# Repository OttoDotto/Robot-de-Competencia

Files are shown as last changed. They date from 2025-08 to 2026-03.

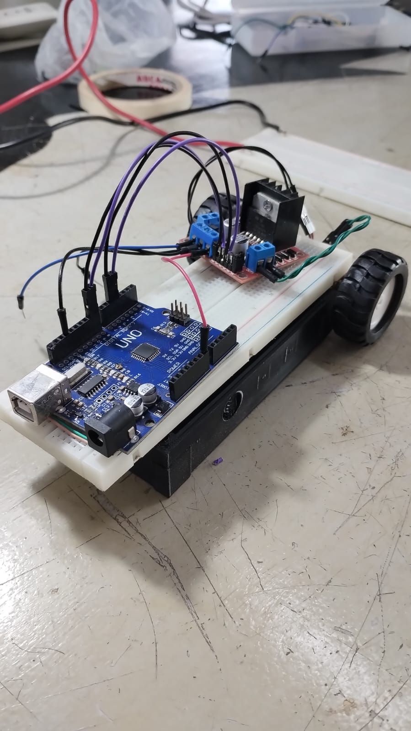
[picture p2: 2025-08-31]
Galeria/prueba_Protoboard - V0.jpg

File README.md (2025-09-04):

# Proyecto Robot de Competencia

Este repositorio contiene el diseño y desarrollo de un **robot móvil autónomo** basado en **ESP32**, pensado para competencias de **seguidores de línea** y adaptable a otras categorías (sumo o fútbol robótico).

## 🏁 Objetivo
Este proyecto representa el **primer paso de la Facultad del Ejército Argentino en el mundo de la robótica competitiva**.  
Más allá del desarrollo técnico, nuestro propósito es:  
- Introducirnos en el ámbito de las competencias robóticas estudiantiles.  
- Presentar a nuestra institución en la comunidad tecnológica.  
- Generar experiencia para futuras participaciones en categorías como seguidor de línea, fútbol robótico y sumo.  
- Sentar las bases para que, en el futuro, la Facultad pueda convertirse en **sede de competencias de robótica**.  

## 🔧 Características principales
- **Microcontrolador**: ESP32 DevKit V1
- **Motores**: 2 × DC Pololu con controladores DRV8833 en configuración paralela
- **Sensores**: Array de 8 sensores reflectivos (QTR-8A)
- **Estructura**: Base y Diseño fabricado en impresión 3D
- **Conectividad**: Bluetooth, Wi-Fi y Control con mando PS
- **Aplicaciones**:  
  - Seguidor de línea (principal)  
  - Adaptación a fútbol robótico

## 📂 Contenido del repositorio
- `/Pcb Kicad` → esquemáticos y PCB en KiCad
- `/Fabricacion` → archivos para fabricacion casera del PCB
- `/Programacion` → códigos utilizados (Motores, Sensores, etc.)
- `/Documentos` → documentación, datasheets, imágenes de referencia del proyecto
- `/Galeria` → Fotografias, videos e imagenes del proyecto

## 📸 Galería (soon tm)

## 👥 Autores
Proyecto desarrollado en la **Facultad del Ejército Argentino** por el equipo **Legión de Ohm**.

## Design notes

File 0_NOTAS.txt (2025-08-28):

git: https://github.com/OttoDotto/Robot-de-Competencia

OBJETIVO PRINCIPAL:	Armar el circuito de control del robot de competencia - Seguidor de linea, Futbolero &/o Sumo
* Separar la lectura en otra PCB
* Separar el diseño 3D aparte de las pcbs 			No hacer un T que sea una placa de cobre entera
* Simplificar el trabajo para el equipo de futbol &/o Sumo

REQUIRIMIENTOS:
* Debe tener espacio para sostener los motores o agarrarlos desde el pcb. (optimizar lugar - como en el caso de los competidores)
* Debe tener entradas para la placa de sensores. Conector plano o molex, recibe la lecturas Analógicas y los alimenta vcc&gnd
* Debe tener tira de pines para quitar o cambiar los puentesH o el uc
* Debe tener cables con un conector para alimentar la pcb
* Debe tener un regulador de tensión para alimentar desde una pila externa mediante un conector (con. cable-cable)
* Si es necesario usaremos componentes SMD
* En el caso del seguidor, vamos a usar:
	* microC	- ESP WROOM-32 DEVKIT V1
	* PUENTE H	- DRV8833			MODO PARALELO			
	* MOTORES	- MICRO POLOLU 6V 500 RPM
* Debe tener pulsadores o botones integrados en el pcb
	- Encendido del robot
	- Calibración de sensores	(leer que valores son blancos y cuales son negros - cambia con la pista)

TO-DO:
* Charlar sobre el presupuesto y tiempo a dedicar + que buscamos conseguir con la competencia	(Aprobar TD2)
* Leer los reglamentos en caso de excepciones con los componentes que usemos
* Buscar y definir que baterias vamos a utilizar
* Definir el tamaño del pcb y chasis (Trapecio)
* Buscar el modelo 3D aprox de los motores
* Buscar y definir que conectores vamos a usar
* Verificar el micro-controlador que estamos usando

DONE:
* Sensores a usar QTR-8A. Pueden trabajar con 3.3V  (Modulo de 8 sensores con 11 pines, vcc y gnd + 8 salidas Analogs + pin apagarleds)

APUNTES:
* Los sensores deben ir conectados a los ADC del ESP32
* Los puentesH deben ir conectados a tres pines, dos de control y uno de pwm
* Vin del esp32 es entre 4 y 12 V

* PINES ESP32 ELEJIDOS:	(D = GPIO !!!!)
Sensores (fila bajo el USB, contiguos para pistas rectas)
S1 → GPIO36 (VP)
S2 → GPIO39 (VN)
S3 → GPIO34
S4 → GPIO35
S5 → GPIO32
S6 → GPIO33
S7 → GPIO27
S8 → GPIO14

Puente H izquierdo (M1) – lado izquierdo del ESP32
IN1_M1 → GPIO26 (PWM)
IN2_M1 → GPIO25 (PWM)
SLEEP_M1 → GPIO16		(PROBLEMA, ESTA DEL OTRO LADO)

Puente H derecho (M2) – lado derecho del ESP32
IN1_M2 → GPIO21 (PWM)
IN2_M2 → GPIO18 (PWM)
SLEEP_M2 → GPIO23

Botones, buzzer, LED (abajo/derecha)
SW1 → GPIO22 (entrada con pull-up interno)
SW2 → GPIO19 (entrada con pull-up interno)
BUZZER → GPIO17 (PWM con LEDC)			(PROBLEMA, queda atrapado)
LED → GPIO13 (salida)

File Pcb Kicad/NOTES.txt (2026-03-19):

OBJETIVO PRINCIPAL:	Armar el circuito de control del robot de competencia - Seguidor de linea, Futbolero &/o Sumo
* Separar la lectura en otra PCB
* Separar el diseño 3D aparte de las pcbs 			No hacer un T que sea una placa de cobre entera
* Simplificar el trabajo para el equipo de futbol &/o Sumo

REQUIRIMIENTOS:
* Debe tener espacio para sostener los motores o agarrarlos desde el pcb. (optimizar lugar - como en el caso de los competidores)
* Debe tener entradas para la placa de sensores. Conector plano o molex, recibe la lecturas Analógicas y los alimenta vcc&gnd + LED_OFF(IR)
* Debe tener tira de pines para quitar o cambiar los puentesH o el uc
* Debe tener un regulador de tensión para alimentar desde una pila externa mediante un conector (con. cable-cable)
* Si es necesario usaremos componentes SMD
* En el caso del seguidor, vamos a usar:
	* microC	- ESP WROOM-32 o Arduino Nano
	* PUENTE H	- DRV8833			
	* MOTORES	- MICRO POLOLU 6V 800 RPM
* Debe tener pulsadores o botones integrados en el pcb
	- Encendido del robot
	- Calibración de sensores	(leer que valores son blancos y cuales son negros - cambia con la pista)

APUNTES:
* PINES ESP32 ELEJIDOS:	(D = GPIO !!!!)
Sensores (fila bajo el USB, contiguos para pistas rectas)
S1 → GPIO36 (VP)
S2 → GPIO39 (VN)
S3 → GPIO34
S4 → GPIO35
S5 → GPIO32
S6 → GPIO33
S7 → GPIO27
S8 → GPIO14

Puente H izquierdo (M1) – lado izquierdo del ESP32
IN1_M1 → GPIO26 (PWM)
IN2_M1 → GPIO25 (PWM)
SLEEP_M1 → GPIO16

Puente H derecho (M2) – lado derecho del ESP32
IN1_M2 → GPIO21 (PWM)
IN2_M2 → GPIO18 (PWM)
SLEEP_M2 → GPIO23

Botones, buzzer, LED (abajo/derecha)
SW1 → GPIO22 (entrada con pull-down)
SW2 → GPIO19 (entrada con pull-down)
BUZZER → GPIO17 (PWM con LEDC)
LED → GPIO13 (salida)

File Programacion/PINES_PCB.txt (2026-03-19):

* PINES ESP32 ELEJIDOS:	(D = GPIO !!!!)

📡 Sensores 
(Fila bajo el USB, contiguos para pistas rectas)
| Sensor |  Pin ESP32  | Descripción |
|---|---|---|
| S1 | GPIO36 (VP) | Entrada analógica |
| S2 | GPIO39 (VN) | Entrada analógica |
| S3 | GPIO34 | Entrada analógica |
| S4 | GPIO35 | Entrada analógica |
| S5 | GPIO32 | Entrada analógica |
| S6 | GPIO33 | Entrada analógica |
| S7 | GPIO27 | Entrada digital |
| S8 | GPIO14 | Entrada digital |

⚙️ Puente H izquierdo (M1)  
(Lado izquierdo del ESP32)
| Señal | Pin ESP32 | Función |
|---|---|---|
| IN1_M1 | GPIO26 | PWM |
| IN2_M1 | GPIO25 | PWM |
| SLEEP_M1  | GPIO16 | Control de habilitación |

⚙️ Puente H derecho (M2)  
(Lado derecho del ESP32)
| Señal | Pin ESP32 | Función |
|---|---|---|
| IN1_M2 | GPIO21 | PWM |
| IN2_M2 | GPIO18 | PWM |
| SLEEP_M2  | GPIO23 | Control de habilitación |

🔘 Botones, 🔔 Buzzer, 💡 LED, 📶 Sensor IR
| Componente | Pin ESP32 | Configuración |
|---|---|---|
| SW1 | GPIO22 | Entrada con pull-down |
| SW2 | GPIO19 | Entrada con pull-down |
| BUZZER | GPIO17 | PWM con LEDC |
| LED | GPIO13 | Salida digital |
| IR | GPIO04 | Entrada con pull-up externo |

📑 Resumen
Este documento lista los pines utilizados en el proyecto con ESP32, organizados por función:  
- Sensores de pista  
- Puentes H para control de motores (M1 y M2)  
- Botones, buzzer, LED y sensor IR

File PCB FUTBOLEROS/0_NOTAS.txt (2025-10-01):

OBJETIVO PRINCIPAL:	Armar el circuito de control del robot de competencia - Seguidor de linea, Futbolero &/o Sumo
* Separar la lectura en otra PCB
* Separar el diseño 3D aparte de las pcbs 			No hacer un T que sea una placa de cobre entera
* Simplificar el trabajo para el equipo de futbol &/o Sumo

REQUIRIMIENTOS:
* Debe tener espacio para sostener los motores o agarrarlos desde el pcb. (optimizar lugar - como en el caso de los competidores)
* Debe tener entradas para la placa de sensores. Conector plano o molex, recibe la lecturas Analógicas y los alimenta vcc&gnd + LED_OFF(IR)
* Debe tener tira de pines para quitar o cambiar los puentesH o el uc
* Debe tener un regulador de tensión para alimentar desde una pila externa mediante un conector (con. cable-cable)
* Si es necesario usaremos componentes SMD
* En el caso del seguidor, vamos a usar:
	* microC	- ESP WROOM-32 DEVKIT V1
	* PUENTE H	- DRV8833			MODO PARALELO			
	* MOTORES	- MICRO POLOLU 6V 500 RPM
* Debe tener pulsadores o botones integrados en el pcb
	- Encendido del robot
	- Calibración de sensores	(leer que valores son blancos y cuales son negros - cambia con la pista)

TO-DO:
* REVISAR EL REGULADOR DE TENSION DE LA PCB (7805 -> AMS1117) 
	- cambiar por regulador Low voltage dropout
	- 7805 SMD son 2V, MINIMO NECESITA 7V y casi 9V
	- AMS1117 SMD son 1.1V, NECESITA 6V Y CASI 7V

* REVISAR LOS BOTONES PULLDOWN (peligroso)
	1. poner una resistencia que vaya al micro
	2. cambiar por un pull down
	3. o usar pull down	(NO USAR EL PUENTE)
	4. cap de 100n (anti-rebote)

* REVISAR COMO CONECTAR LA ALIMENTACION
	- SISTEMA ANTI-PUJOL
	- CONECTOR "POLARIZADO"
	- DIODO SHOCKY EN DIRECTA

* SISTEMA MEDIDOR DE NIVEL DE BATERIA
	- Divisor de tension (8.4 a 3.3 [3.2] Volts) + Diodos de protec (BTA) o diodos simples + CAP
	- Tambien es protec de sobretension (version 2)
	- TEST POINTS [mas facil]

* Buscar el modelo 3D aprox de los motores
* Buscar y definir que conectores vamos a usar (TIRA DE PINES + )

DONE:
* Leer los reglamentos en caso de excepciones con los componentes que usemos
* Sensores a usar QTR-8A. Pueden trabajar con 3.3V  (Modulo de 8 sensores con 11 pines, vcc y gnd + 8 salidas Analogs + pin apagarleds)
* Charlar sobre el presupuesto y tiempo a dedicar + que buscamos conseguir con la competencia	(Aprobar TD2)
* Buscar y definir que baterias vamos a utilizar
* Definir el tamaño del pcb y chasis (Trapecio)
* Verificar el micro-controlador que estamos usando	(ESP WROOM 32 - DEVKIT V1 - USB C y B)

APUNTES:
* Los sensores deben ir conectados a los ADC del ESP32
* Los puentesH deben ir conectados a tres pines, dos de control y uno de pwm
* Vin del esp32 es entre 4 y 12 V
* PINES ESP32 ELEJIDOS:	(D = GPIO !!!!)
Sensores (fila bajo el USB, contiguos para pistas rectas)
S1 → GPIO36 (VP)
S2 → GPIO39 (VN)
S3 → GPIO34
S4 → GPIO35
S5 → GPIO32
S6 → GPIO33
S7 → GPIO27
S8 → GPIO14

Puente H izquierdo (M1) – lado izquierdo del ESP32
IN1_M1 → GPIO26 (PWM)
IN2_M1 → GPIO25 (PWM)
SLEEP_M1 → GPIO16

Puente H derecho (M2) – lado derecho del ESP32
IN1_M2 → GPIO21 (PWM)
IN2_M2 → GPIO18 (PWM)
SLEEP_M2 → GPIO23

Botones, buzzer, LED (abajo/derecha)
SW1 → GPIO22 (entrada con pull-down)
SW2 → GPIO19 (entrada con pull-down)
BUZZER → GPIO17 (PWM con LEDC)
LED → GPIO13 (salida)

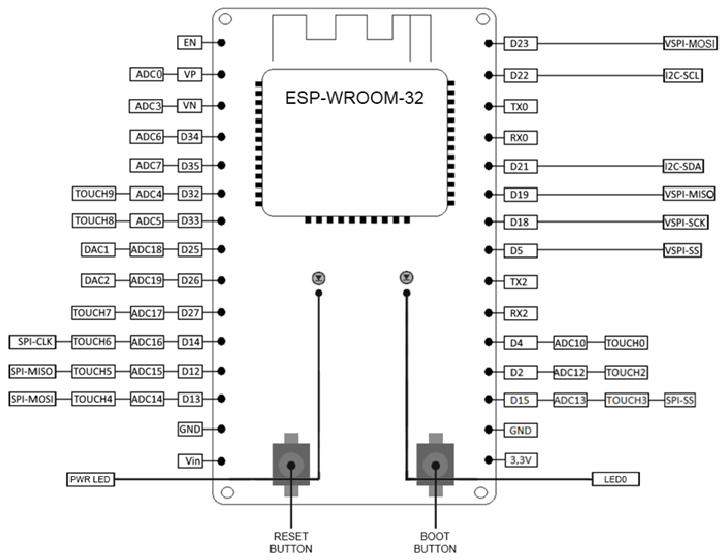
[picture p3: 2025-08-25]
Documentos/ESP32 PINOUT.png

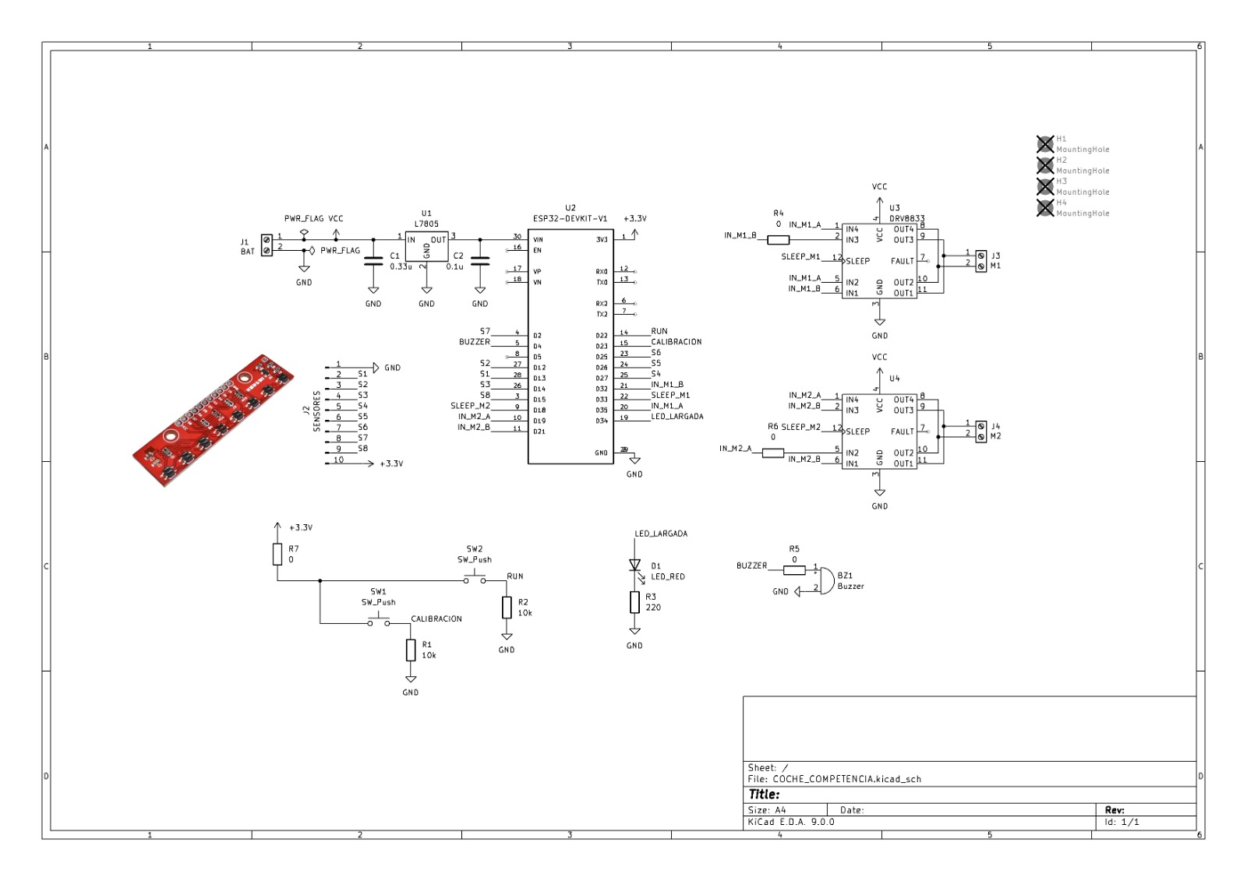
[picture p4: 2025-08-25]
Galeria/V1 SCH.jpeg

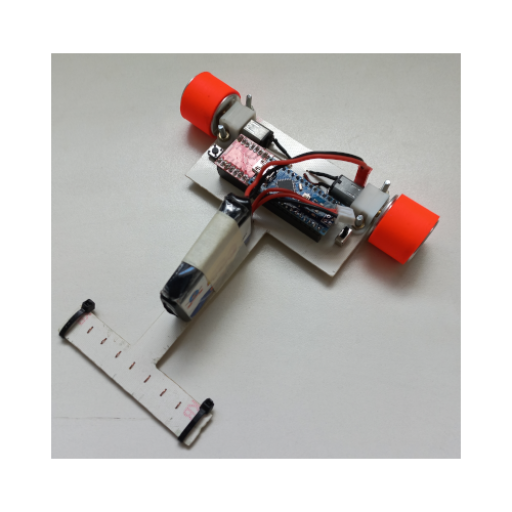
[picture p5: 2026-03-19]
Pcb Kicad/REF GANADORES/1759777126-rqmjTaP9UA.png

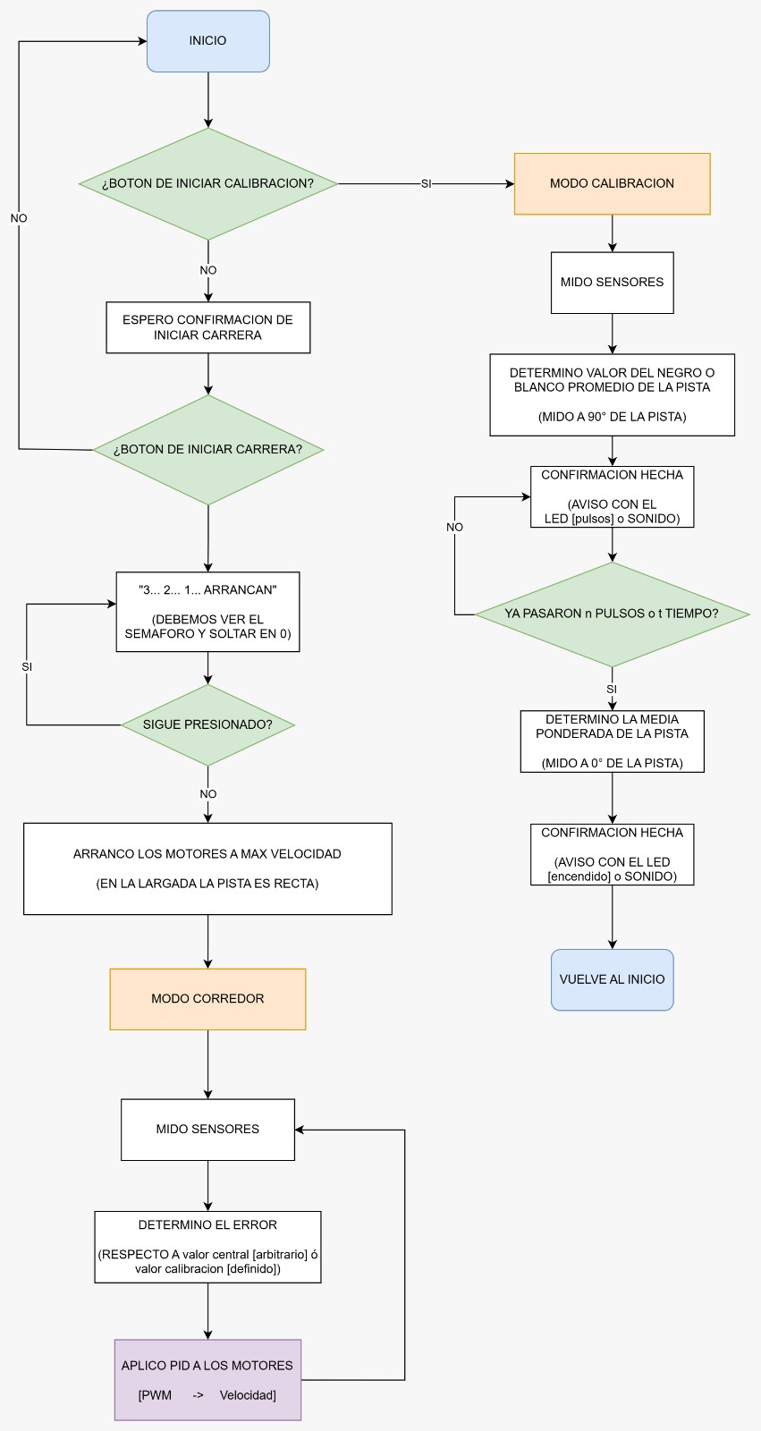
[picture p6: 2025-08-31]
Galeria/FLUJO V1 (CARRERA).jpg

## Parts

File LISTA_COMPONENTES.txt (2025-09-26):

LISTA COMPONENTES X VERSION

V1.0			(95x65 mm)
* ESP WROOM-32 DEVKIT V1
* MODULO DRV8833 
* TIRA DE PINES HEMBRA 2.54 mm
* TIRA DE PINES MACHO 2.54 mm VERTICAL
* REGULADOR 7805 SMD N2
* R smd 0, 220, 10K
* C smd 10n y 330n
* BORNERA DE 2 ENTRADAS
* SWITCH 5 mm 4 PINES
* BUZZER PASIVO
* MODULO QTR-8A
* MOTORES POLOLU 6V - 500 RPM
* BATERIAS 18650

V1.1			(95x63 mm)
(IDEM V1.0- CAMBIO DE TAMANIO DE PCB)

V1.2			(95x63 mm)
* ESP WROOM-32 DEVKIT V1			x1
* MODULO DRV8833 				x2		
* TIRA DE PINES HEMBRA 2.54 mm VERTICAL		(30+12+12)x2
* TIRA DE PINES MACHO 2.54 mm VERTICAL		(5)x1
* TIRA DE PINES MACHO 2.54 mm HORIZONTAL	(12)x1
* REGULADOR AMS1117 SMD N2 - 5V			x1
* R smd 0					x3
* R smd 220					x1
* R smd 1K					x1
* C smd 100n					x3
* C smd 1uf					x1
* BORNERA DE 2 ENTRADAS				x1
* SWITCH 5 mm 4 PINES				x2
* DIODO 1N4148					x1
* TRANSISTOR 2N3904				x1
* BUZZER PASIVO					x1
* MODULO QTR-8A					x1
* MOTOR POLOLU 6V - 1000 o 500 RPM		x2
* BATERIAS 18650				x2

V1.3			(95x63 mm)
* ESP WROOM-32 DEVKIT V1			x1
* MODULO DRV8833 				x2		
* TIRA DE PINES HEMBRA 2.54 mm VERTICAL		(30+12+12)x2
* TIRA DE PINES MACHO 2.54 mm VERTICAL		(5)x1
* TIRA DE PINES MACHO 2.54 mm HORIZONTAL	(12)x1
* REGULADOR AMS1117 SMD N2 - 5V			x1
* R smd 0					x3
* R smd 220					x1
* R smd 100					x2
* R smd 1K					x3
* C smd 100n					x3
* C smd 1uf					x1
* BORNERA DE 2 ENTRADAS				x3
* SWITCH 5 mm 4 PINES				x2
* DIODO SCHOCKY 1N5822 (3 AMPS)			x1
* DIODO 1N4148					x1
* TRANSISTOR 2N3904				x1
* BUZZER PASIVO					x1
* MODULO QTR-8A					x1
* MOTOR POLOLU 6V - 1000 RPM			x2
* BATERIAS 18650				x2

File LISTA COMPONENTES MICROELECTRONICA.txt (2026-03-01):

LISTA COMPONENTES MICROELECTRONICA

https://www.microelectronicash.com/tph1x40-eco--det--TPH1X40-ECO

https://www.microelectronicash.com/tpb1x40--det--TPB1X40

https://www.microelectronicash.com/regulador-smd-5v-1amp-d2pack--det--LM7805SMD

https://www.microelectronicash.com/r1206-0--det--R1206-0

https://www.microelectronicash.com/r1206-220--det--R1206-220

https://www.microelectronicash.com/r1206-100--det--R1206-100

https://www.microelectronicash.com/r1206-1k--det--R1206-1K

https://www.microelectronicash.com/r1206-10k--det--R1206-10K

https://www.microelectronicash.com/c1206-0-01--det--C1206-0.01

https://www.microelectronicash.com/c1206-1uf--det--C1206-1UF

https://www.microelectronicash.com/1n4148--det--1N4148

https://www.microelectronicash.com/b2p--det--B2P

https://www.microelectronicash.com/ts4-5--det--TS4-5

https://www.microelectronicash.com/1n5822--det--1N5822

ADJUNTO DATOS DE FACTURACION:
FUNDACIÓN
Razón Social: Fundación Gral. D Manuel N. Savio
Domicilio: Av. Cabildo 15 - CP:1426
CUIT: 30-69062254-4
Condición de IVA: Exento
Factura B o C

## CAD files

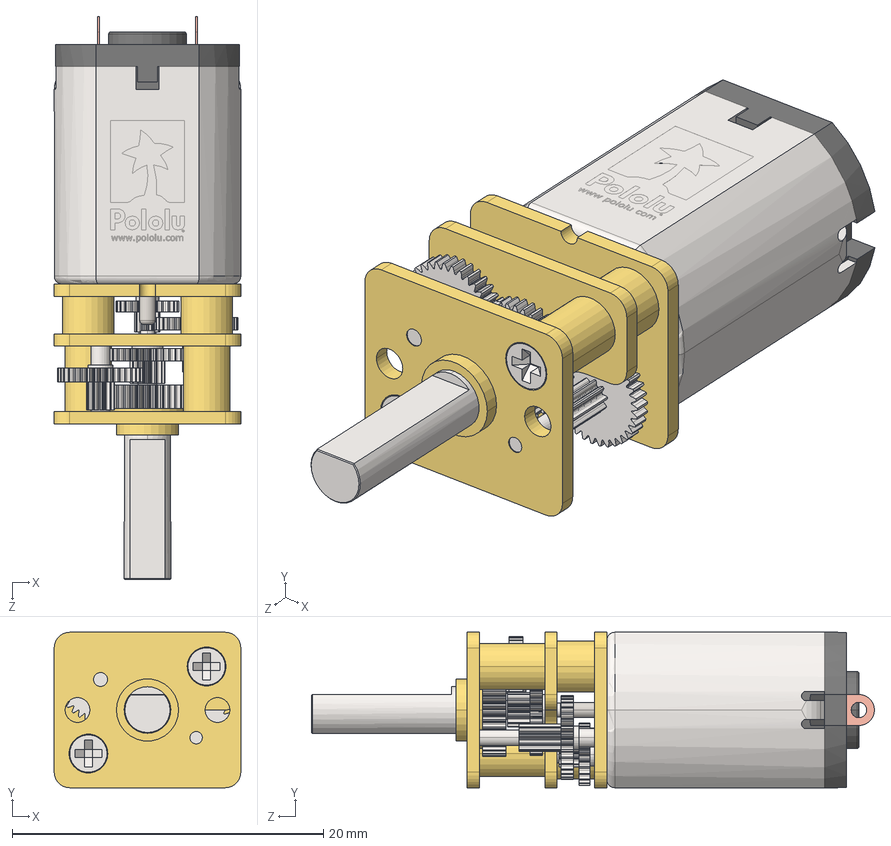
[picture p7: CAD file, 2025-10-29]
Motores Kicad/Pololu/mmgm-cb.step
12.0 x 10.0 x 36.2 mm

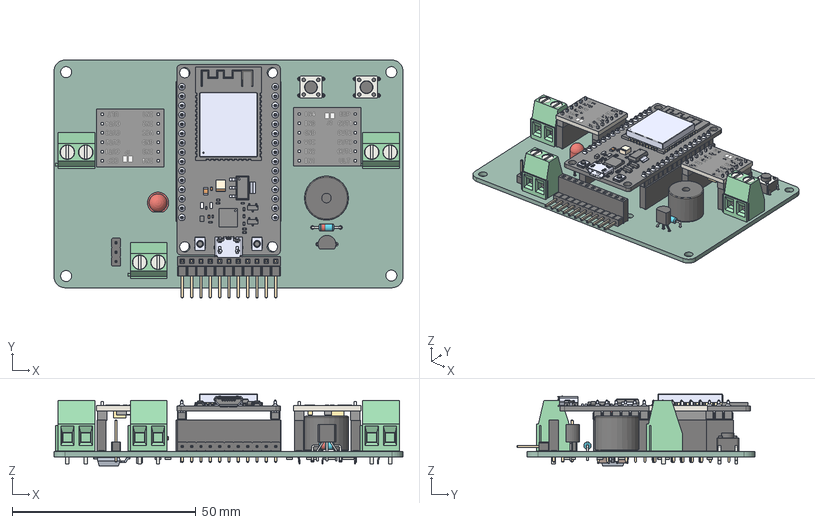
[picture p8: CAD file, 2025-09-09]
PCB FUTBOLEROS/COCHE_COMPETENCIA.step
95.0 x 64.8 x 19.6 mm
PinHeader_1x11_P2.54mm_Horizontal
PinSocket_1x11_P2.54mm_Vertical
SW_PUSH_6mm_H5mm x 2
TerminalBlock_Phoenix_MKDS-1,5-2_1x02_P5.00mm_Horizontal x 3
PinHeader_1x03_P2.54mm_Vertical
ESP32-DEVKIT-V1
PinSocket_1x15_P2.54mm_Vertical x 2
LED_D5.0mm
HBridgeDRV8833 x 2
PinSocket_1x06_P2.54mm_Vertical x 4
MagneticBuzzer_ProSignal_ABI-009-RC
TO-92_Inline_Wide
D_DO-35_SOD27_P7.62mm_Horizontal
R_1206_3216Metric x 7
C_1206_3216Metric x 2
COCHE_COMPETENCIA 1.29.1
COCHE_COMPETENCIA_PCB

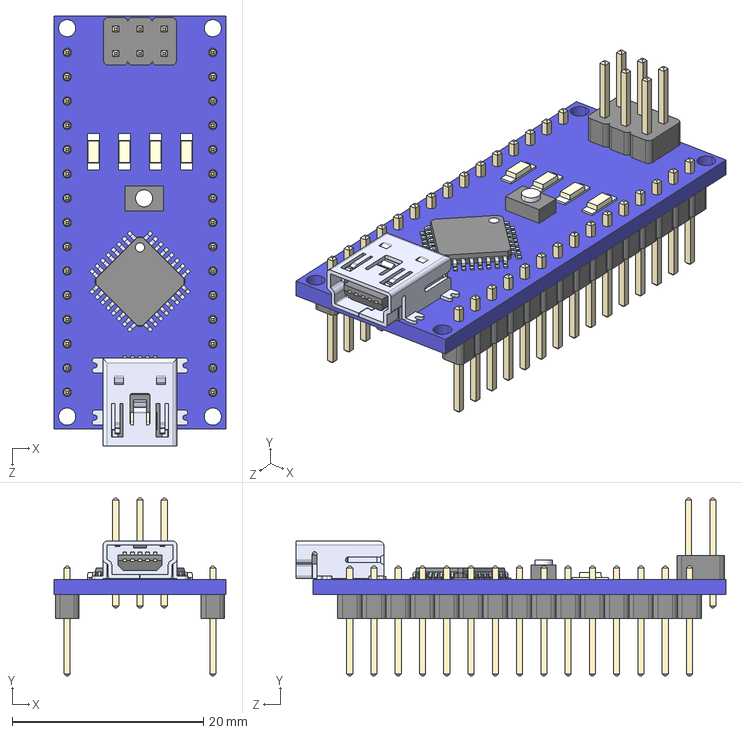
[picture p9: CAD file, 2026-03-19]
Pcb Kicad/include/Arduino NANO/ARDUINO_NANO.step
18.0 x 18.6 x 45.0 mm

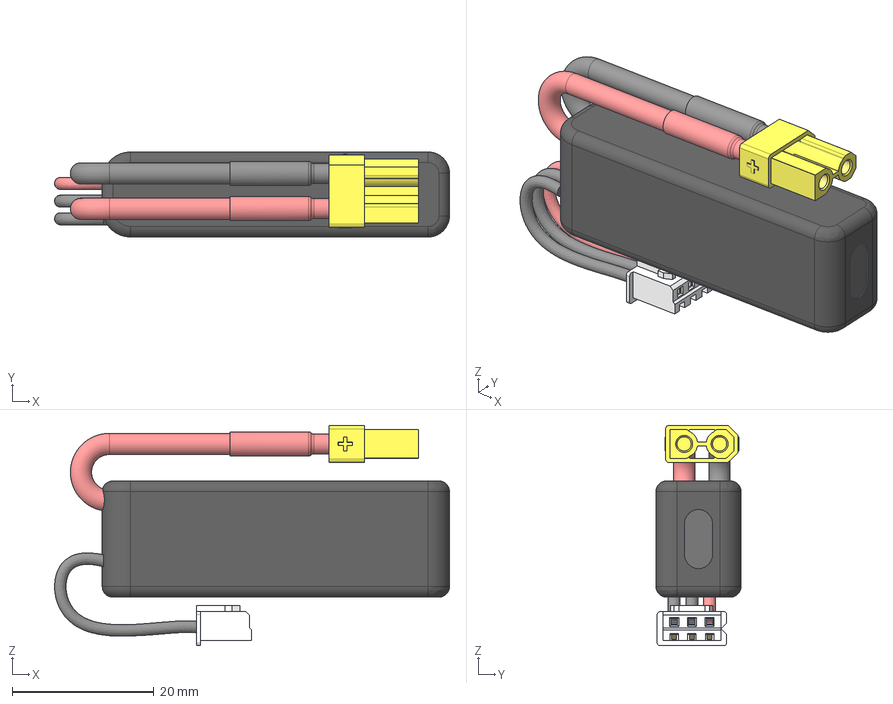
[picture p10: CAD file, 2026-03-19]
Pcb Kicad/include/Bateria 9S/GNB3502S70AHV 18g v1.step
55.7 x 12.0 x 31.1 mm
16GA (XT30) v1 (1)
Heat Shrink (1)
16GA (XT30)
XHP-3 2S v1

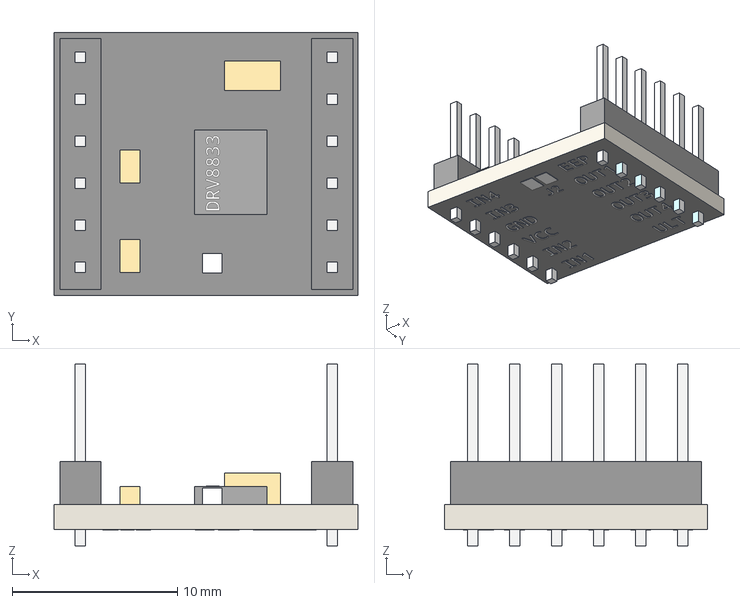
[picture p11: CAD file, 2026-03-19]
Pcb Kicad/include/DRV8833/HBridgeDRV8833.step
18.4 x 15.9 x 11.0 mm

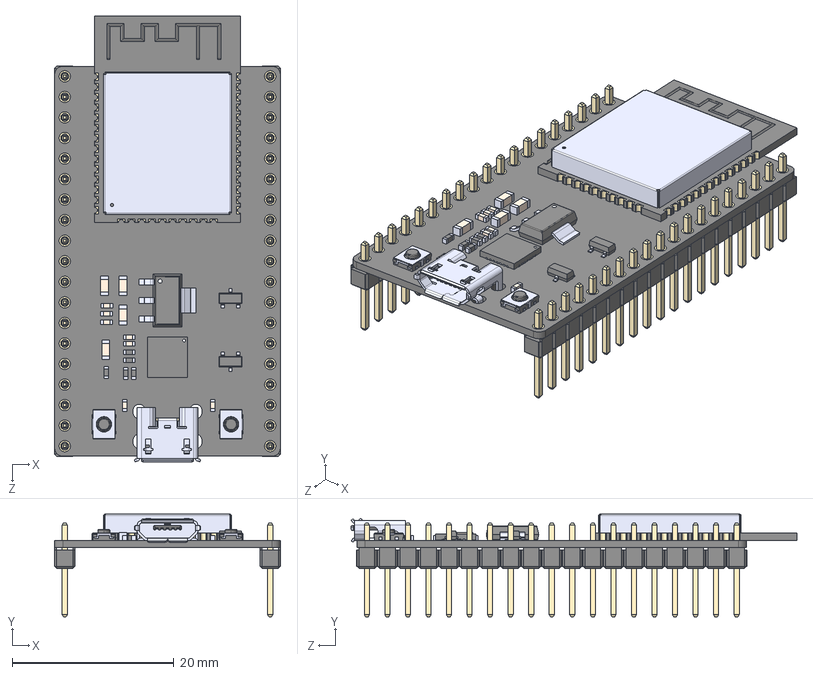
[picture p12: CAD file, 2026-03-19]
Pcb Kicad/include/esp32 devkit/ESP32-DEVKITC-32E--3DModel-STEP-269445.STEP
27.9 x 12.7 x 55.1 mm
board
header x 2
ESP32-WROOM-32D
micro usb
button x 2
CP2102N-A01-GQFN28
AMS1117-3.3
SS8050-G
components^DEVKIT V1 ESP32-WROOM-32

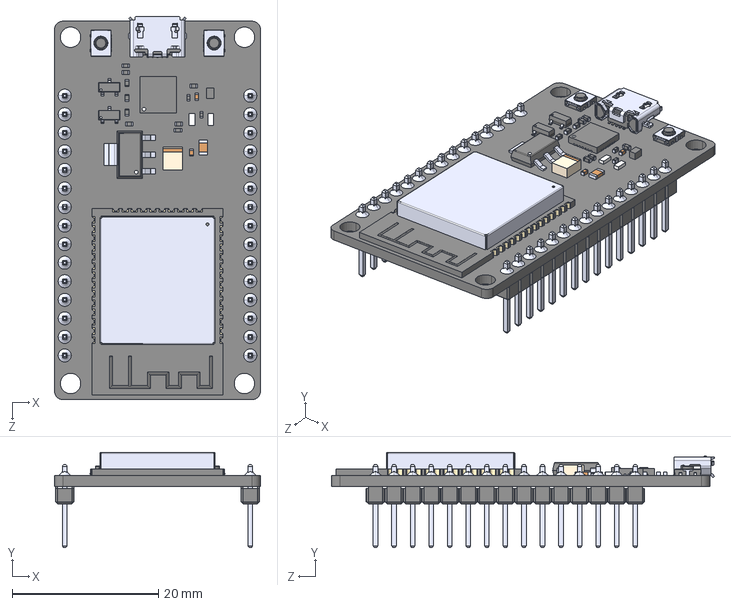
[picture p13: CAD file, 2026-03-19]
Pcb Kicad/include/ESP32-DEVKIT-V1/ESP32-DEVKIT-V1.step
28.2 x 13.1 x 52.5 mm

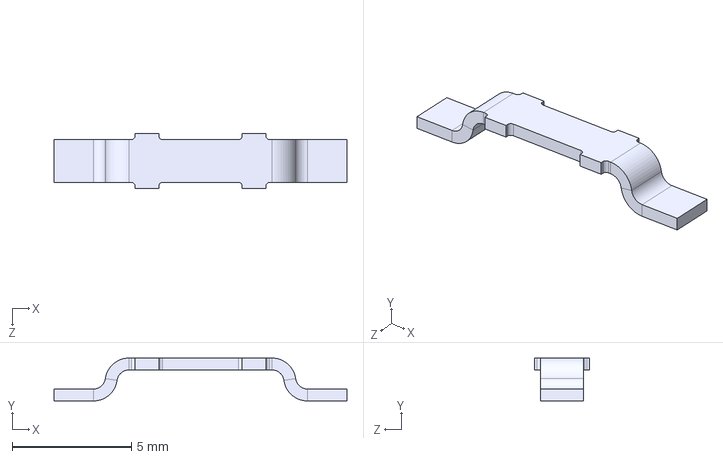
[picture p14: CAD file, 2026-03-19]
Pcb Kicad/include/JUMPLER 5104/5104--3DModel-STEP-630548.STEP
12.3 x 1.80 x 2.30 mm

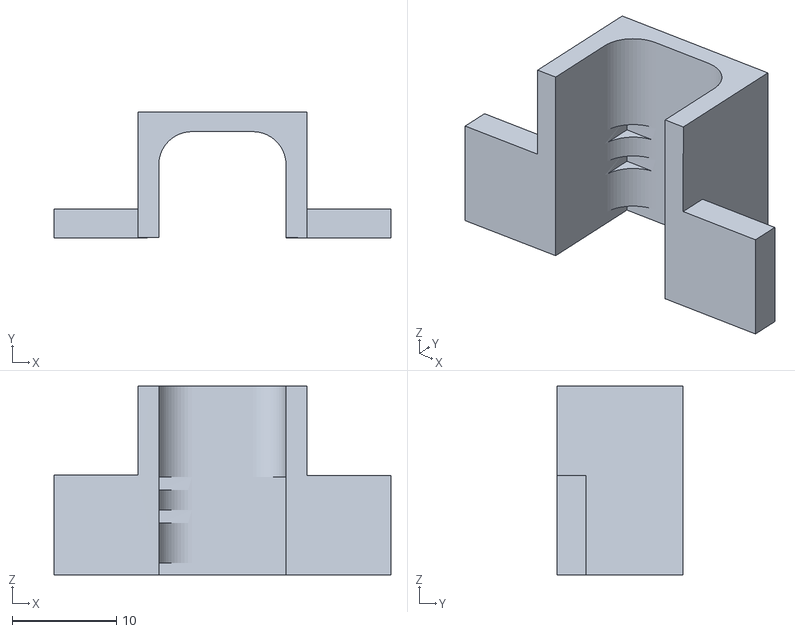
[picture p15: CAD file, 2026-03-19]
Pcb Kicad/include/Pololu/gearmotor_b1r.stl
32.3 x 12.1 x 18.1

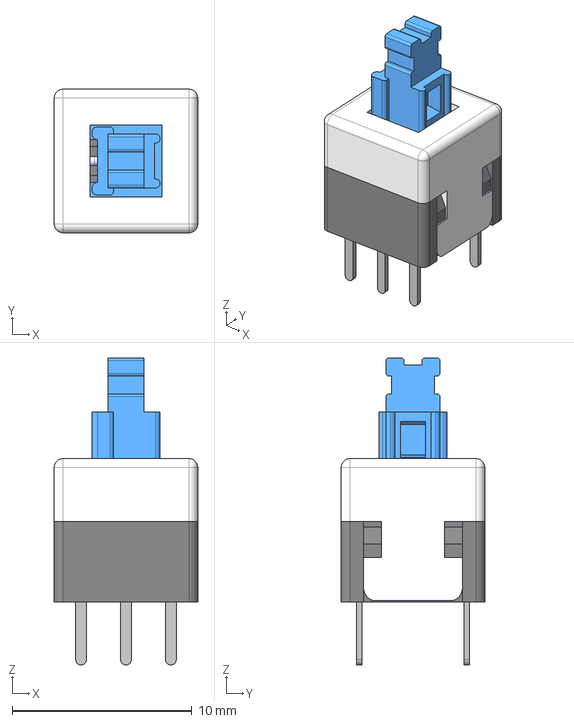
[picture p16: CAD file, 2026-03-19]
Pcb Kicad/include/SWITCH 6P/Push Switch_8x8_6pin_with Lock.stp
8.00 x 8.00 x 17.1 mm

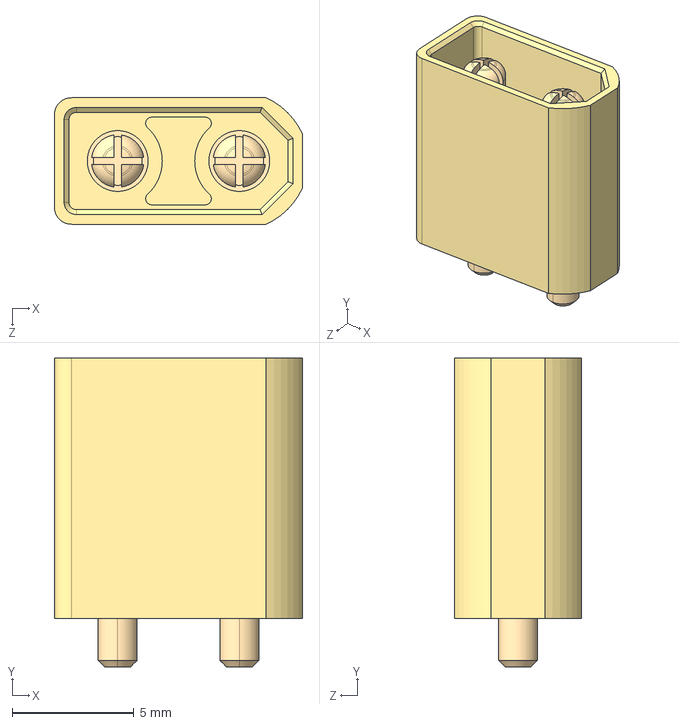
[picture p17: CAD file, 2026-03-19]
Pcb Kicad/include/XT60-M/XT30UPB-M--3DModel-STEP-510211.STEP
10.2 x 12.7 x 5.20 mm

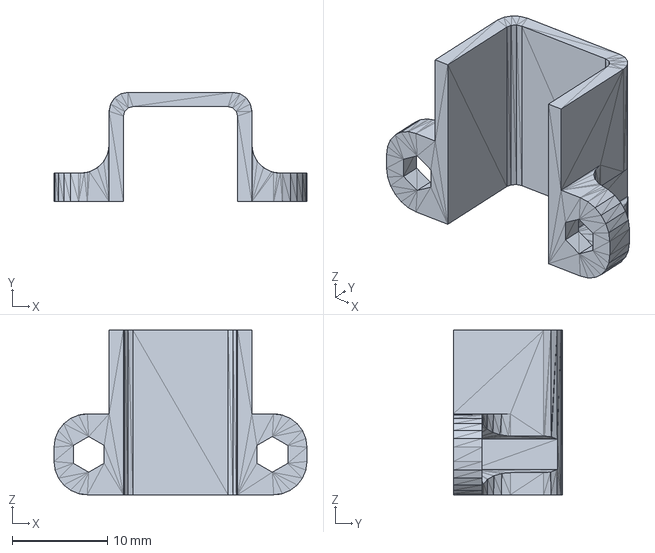
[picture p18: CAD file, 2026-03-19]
Pcb Kicad/include/Pololu/AnyConv.com__motor_housing.step
26.6 x 11.5 x 17.3 mm

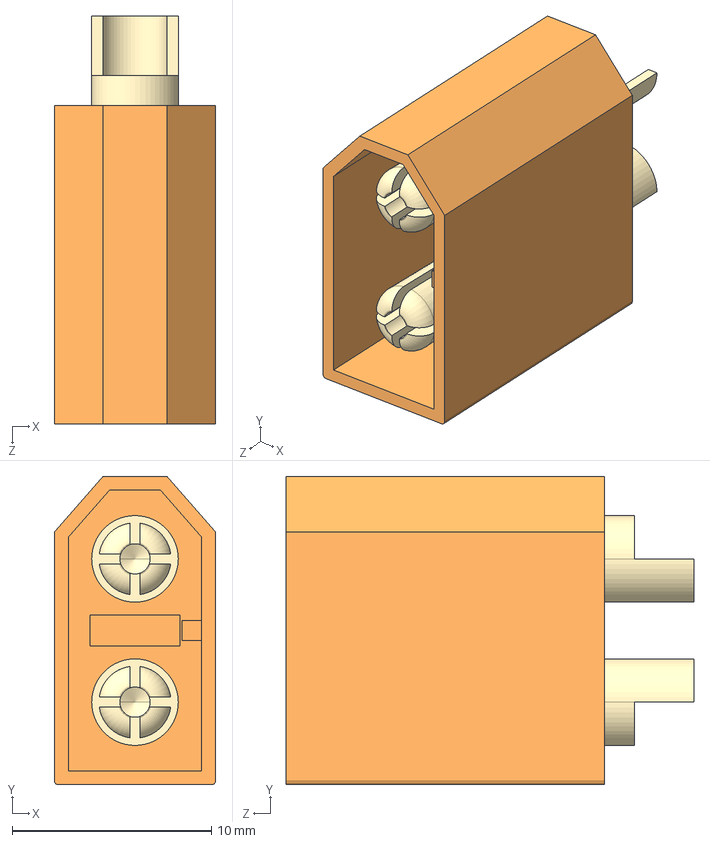
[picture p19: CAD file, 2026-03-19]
Pcb Kicad/include/XT60-M/XT60-M.step
8.10 x 15.5 x 20.5 mm

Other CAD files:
Motores Kicad/Pololu/mmgm-pm.step

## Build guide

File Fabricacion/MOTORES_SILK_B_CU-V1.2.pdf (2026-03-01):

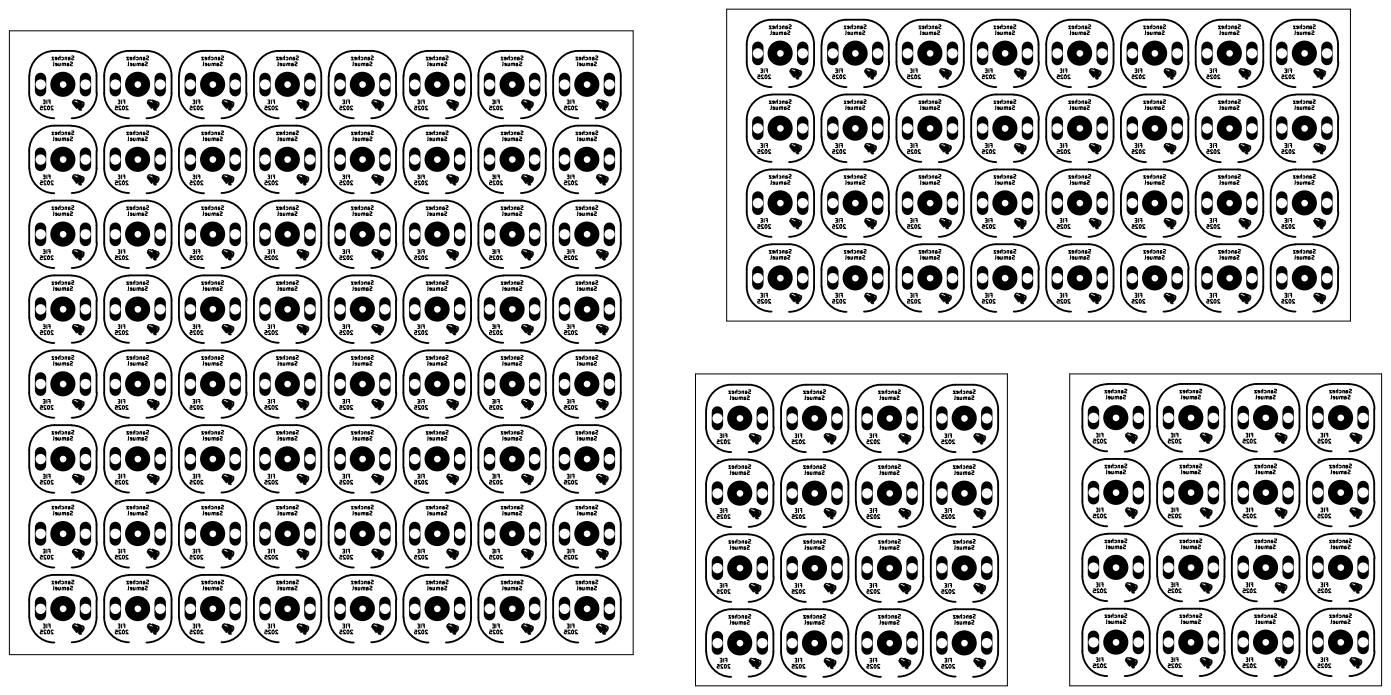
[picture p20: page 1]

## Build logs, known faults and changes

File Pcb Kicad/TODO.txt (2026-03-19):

* WIP - REEMPLAZAR esp32 por un Arduino nano
	- achica la pcb, facilita la decision de pines y capaz es un trazado mas facil...

* Hacer huella de bateria 9s (3s en el ESQ)

* Buscar el modelo 3D aprox de los motores y Bateria

* Buscar el nombre del conector de baterias 9s

* REVISAR COMO CONECTAR LA ALIMENTACION
	- SISTEMA ANTI-PUJOL
	- CONECTOR "POLARIZADO" (baterias 9S)
	- DIODO SHOCKY EN DIRECTA

* Fabricacion china?
	- samu: estando en 5to al menos debemos saber/aprender como pedir plaquetas afuera...
	- en jlcpcb dicen que estan baratisimas, por ejemplo las placas de 4 capas son solo 2 dolares!
	- Podriamos hacer pistas mas chicas y planos de alimentacion y de masa, achicando mas la placa

* Basado en la sig. pieza, se puede colocar en el pcb como si fueran los motores?
	https://www.thingiverse.com/thing:2543948

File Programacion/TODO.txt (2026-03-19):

1. MODULO MOTORES:
    El programa pierde tiempo al usar clases y objetos en los motores, reemplazar por funciones y variables

2. Comentarios y Notas Makefile
    El programa tenia un makefile pero hace que sea dificil de leer el codigo
    De hecho es 80% comentarios, 20% codigo

3. Sintonizacion PID:
    Si existiera un trimmer o potenciometro es posible ajustar finamente el Ku
    De ser posible tambien se podria usar para sintonizar y despues leer que valor tiene
    
4. SELECCION DE CORREDOR
    Posiblemente se pueda sacar del config y del platformio
    talvez pasarlo a un modulo para facilitar la compilacion
    (Ajusta la vel base [+- correccion] y ctes PID)

5. MAIN:
    Quedaron algunas variables como la velocidad max, una variable stop y la zona muerta
    Posiblemente se deben mover variables a otros modulos de forma que se entienda donde estan

69. Extra - MAIN:
    El programa funciona bien con la maquina de estados, es una maravilla y funciona excelente
    pero es dificil de leer, puede asustar si no se entiende como se ejecuta por dentro la transicion
    Capaz unos dibujos o alguna explicacion puede hacer que no pase eso (sumado al punto 3)

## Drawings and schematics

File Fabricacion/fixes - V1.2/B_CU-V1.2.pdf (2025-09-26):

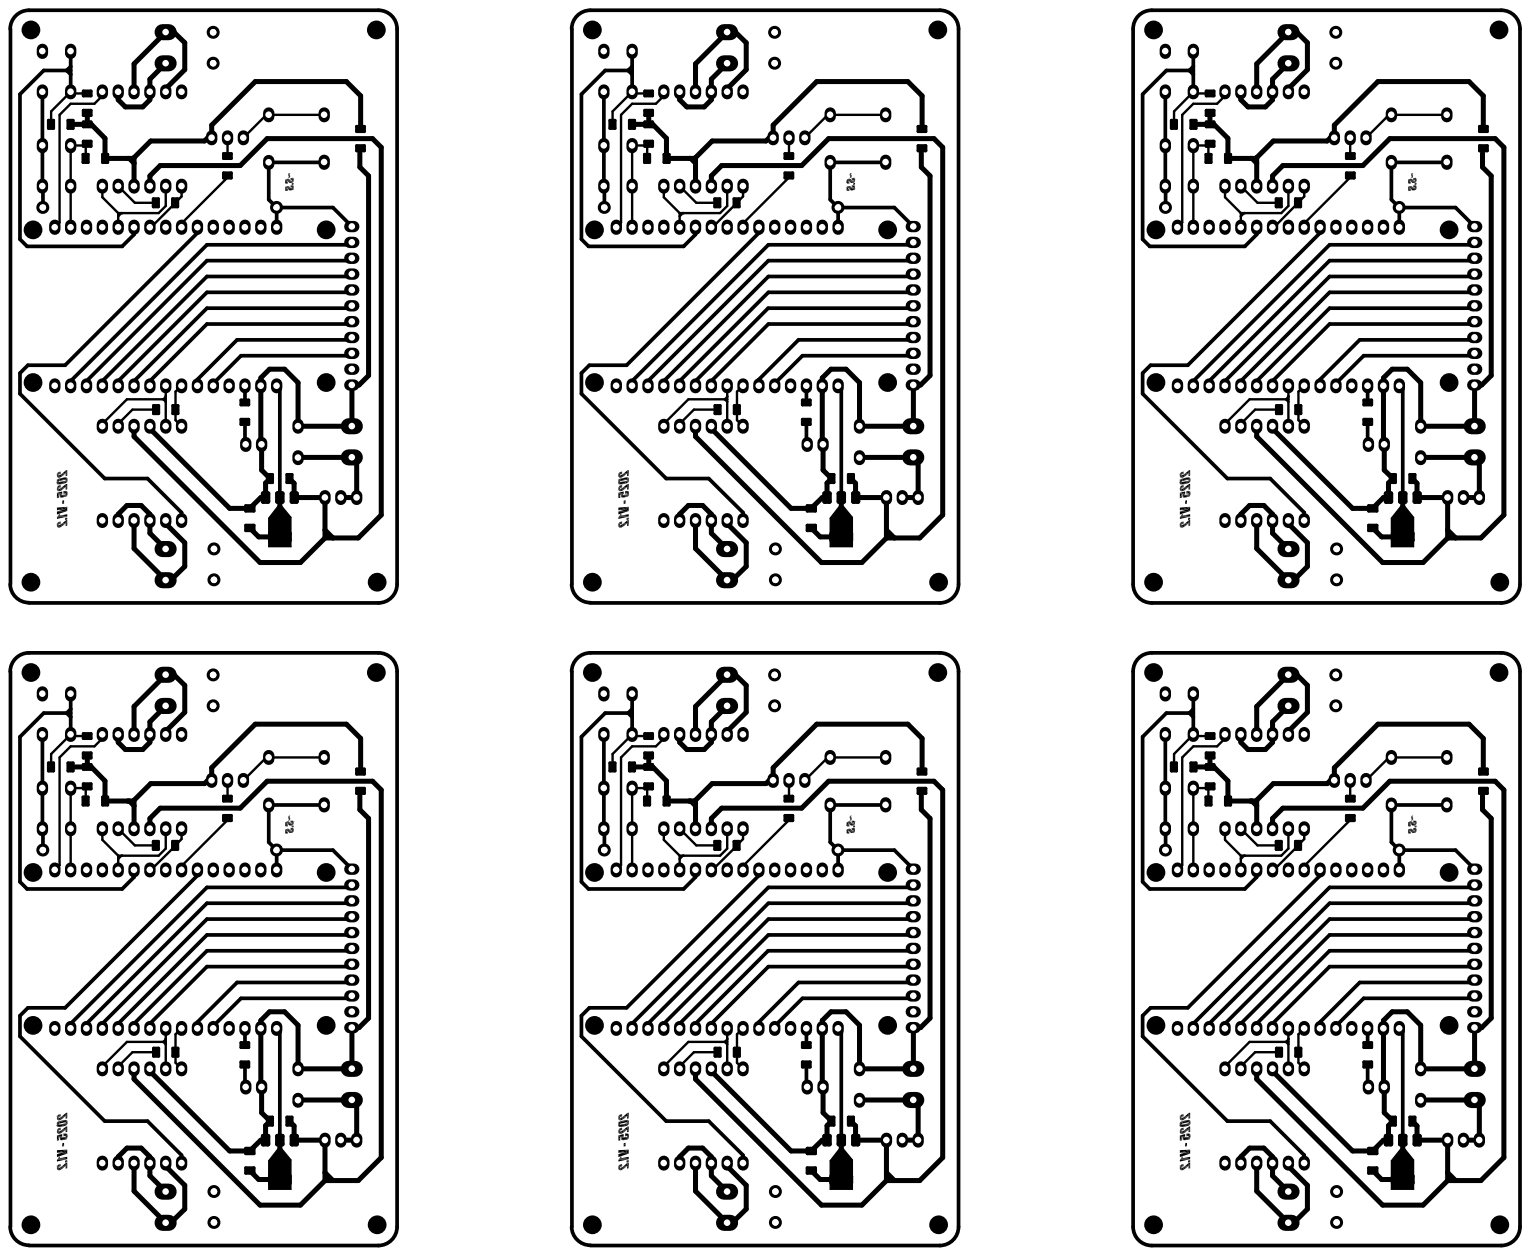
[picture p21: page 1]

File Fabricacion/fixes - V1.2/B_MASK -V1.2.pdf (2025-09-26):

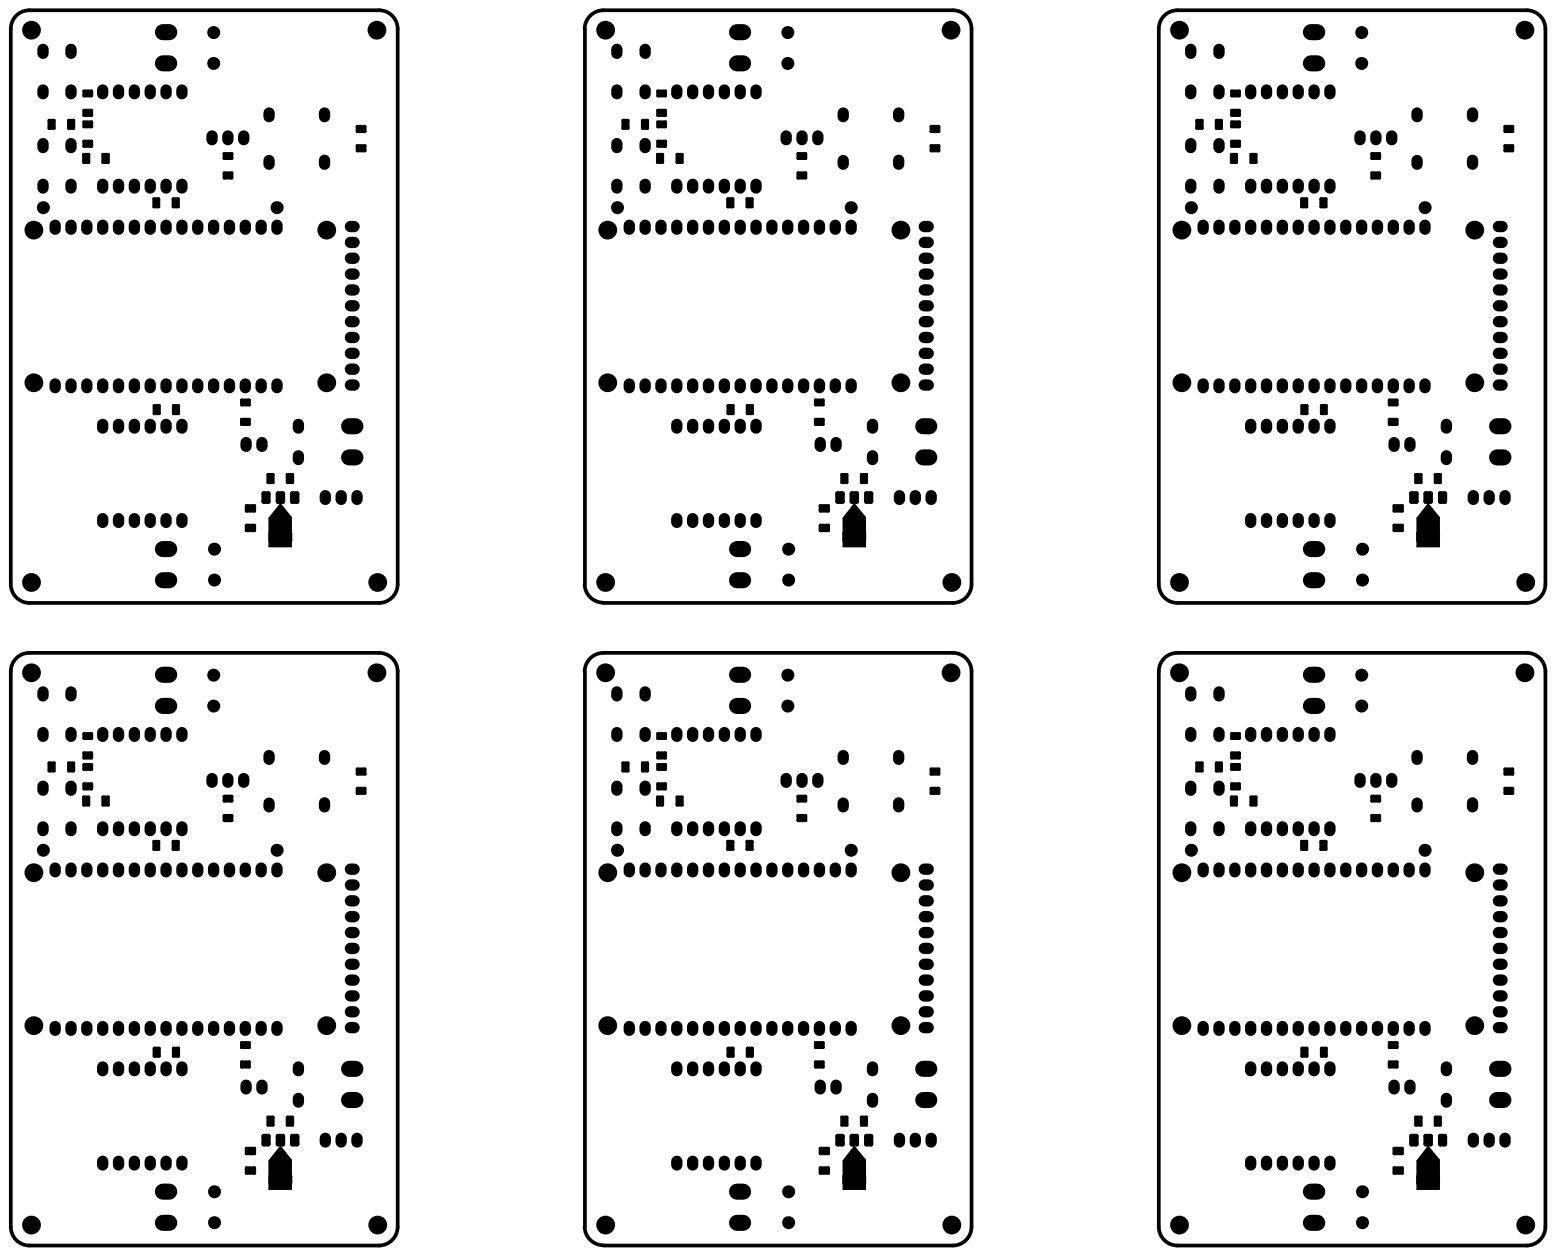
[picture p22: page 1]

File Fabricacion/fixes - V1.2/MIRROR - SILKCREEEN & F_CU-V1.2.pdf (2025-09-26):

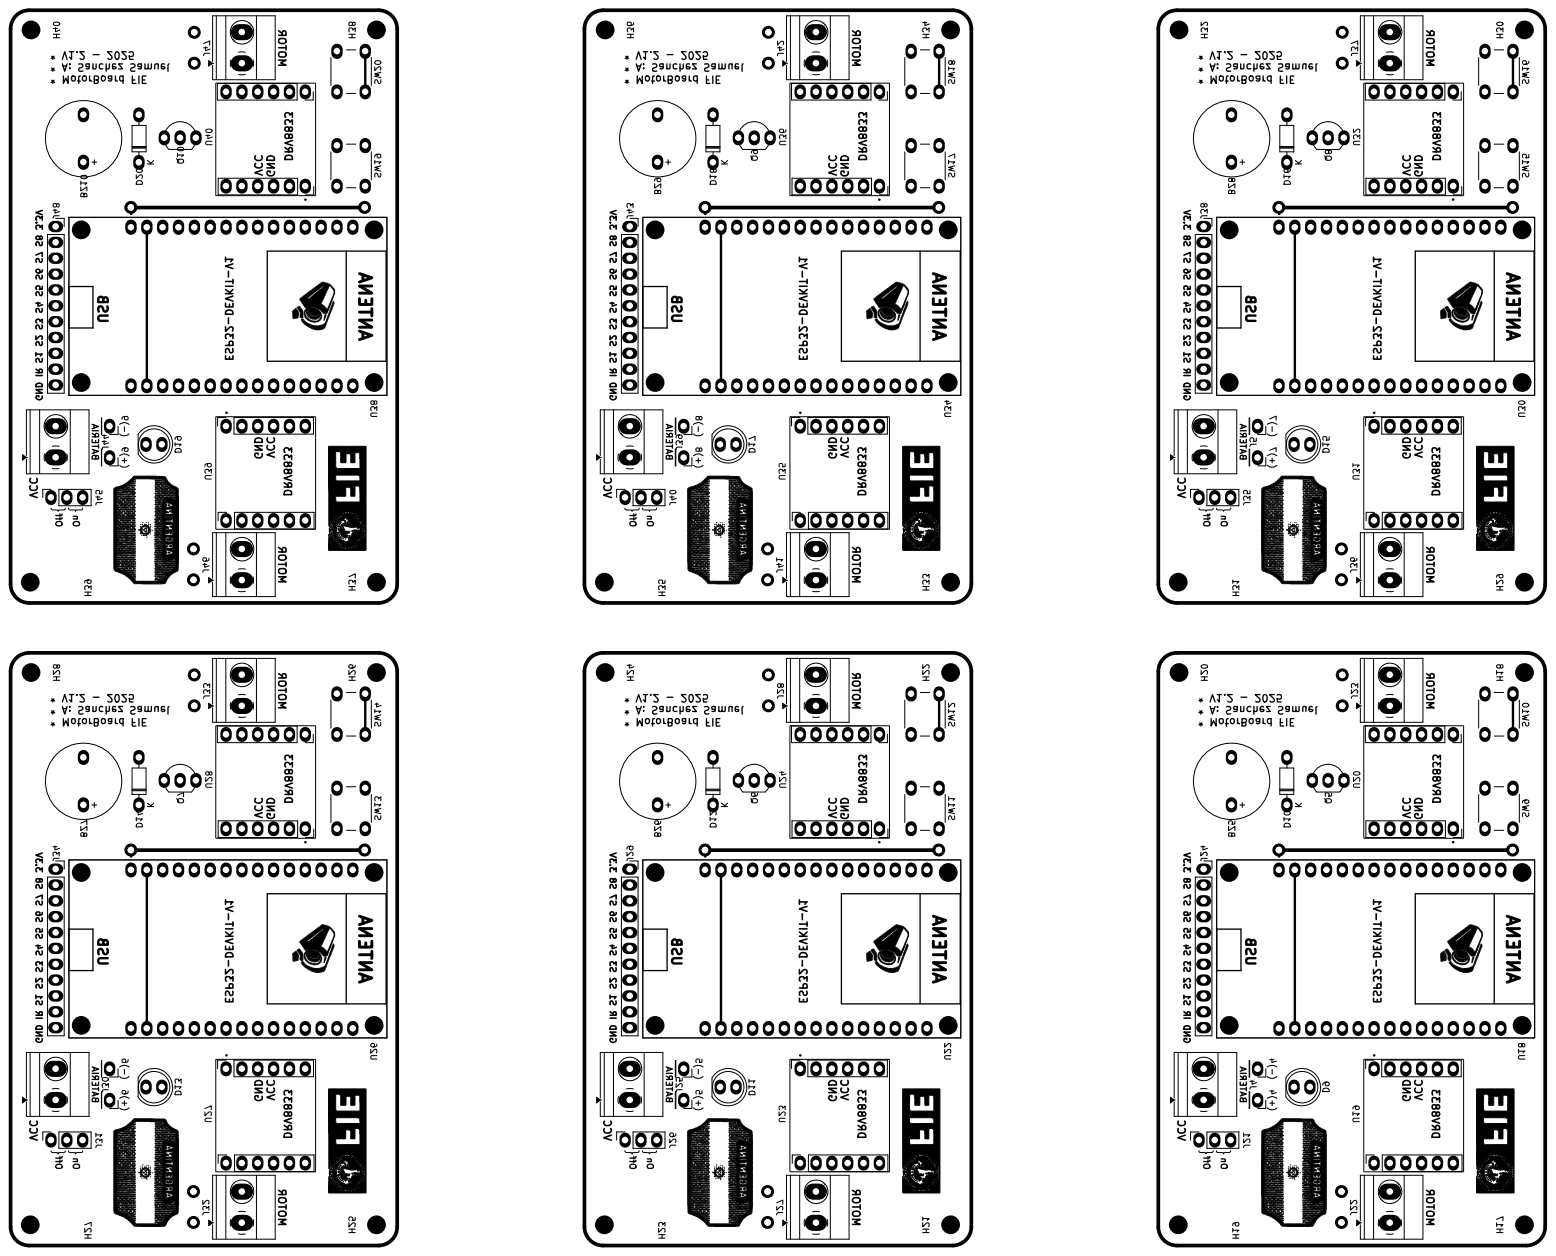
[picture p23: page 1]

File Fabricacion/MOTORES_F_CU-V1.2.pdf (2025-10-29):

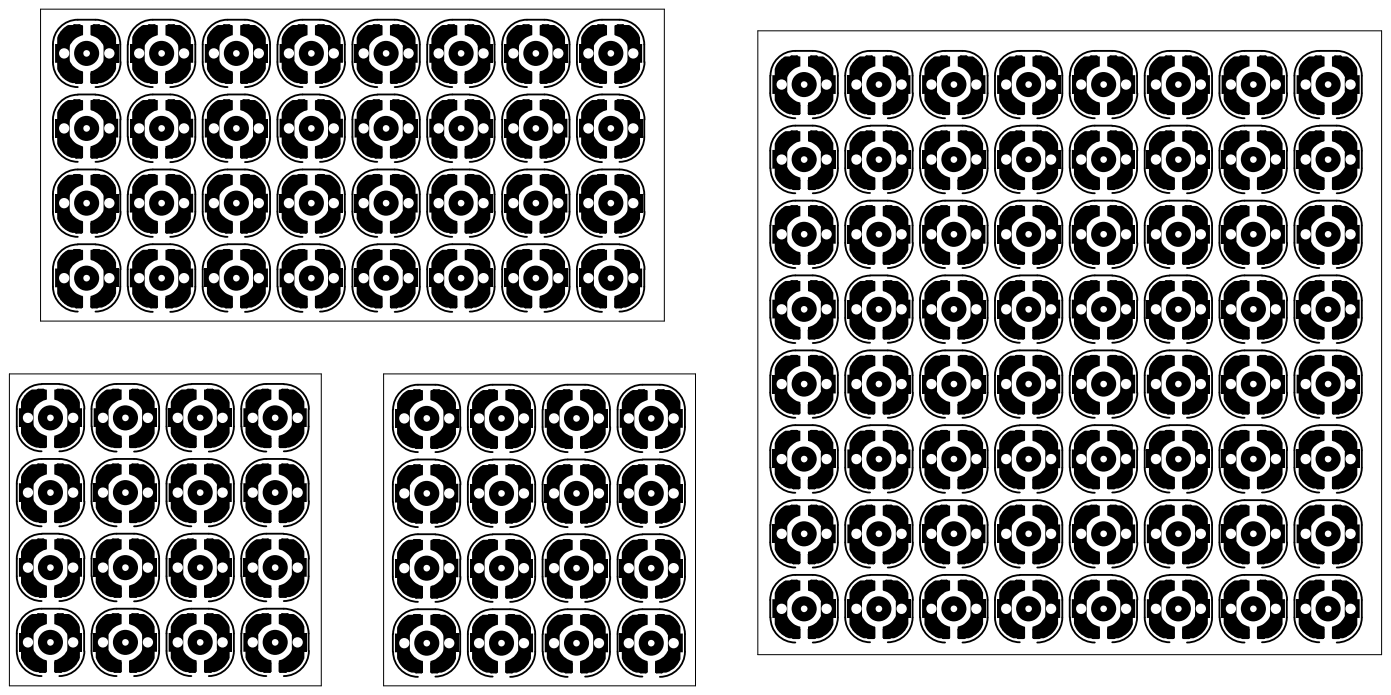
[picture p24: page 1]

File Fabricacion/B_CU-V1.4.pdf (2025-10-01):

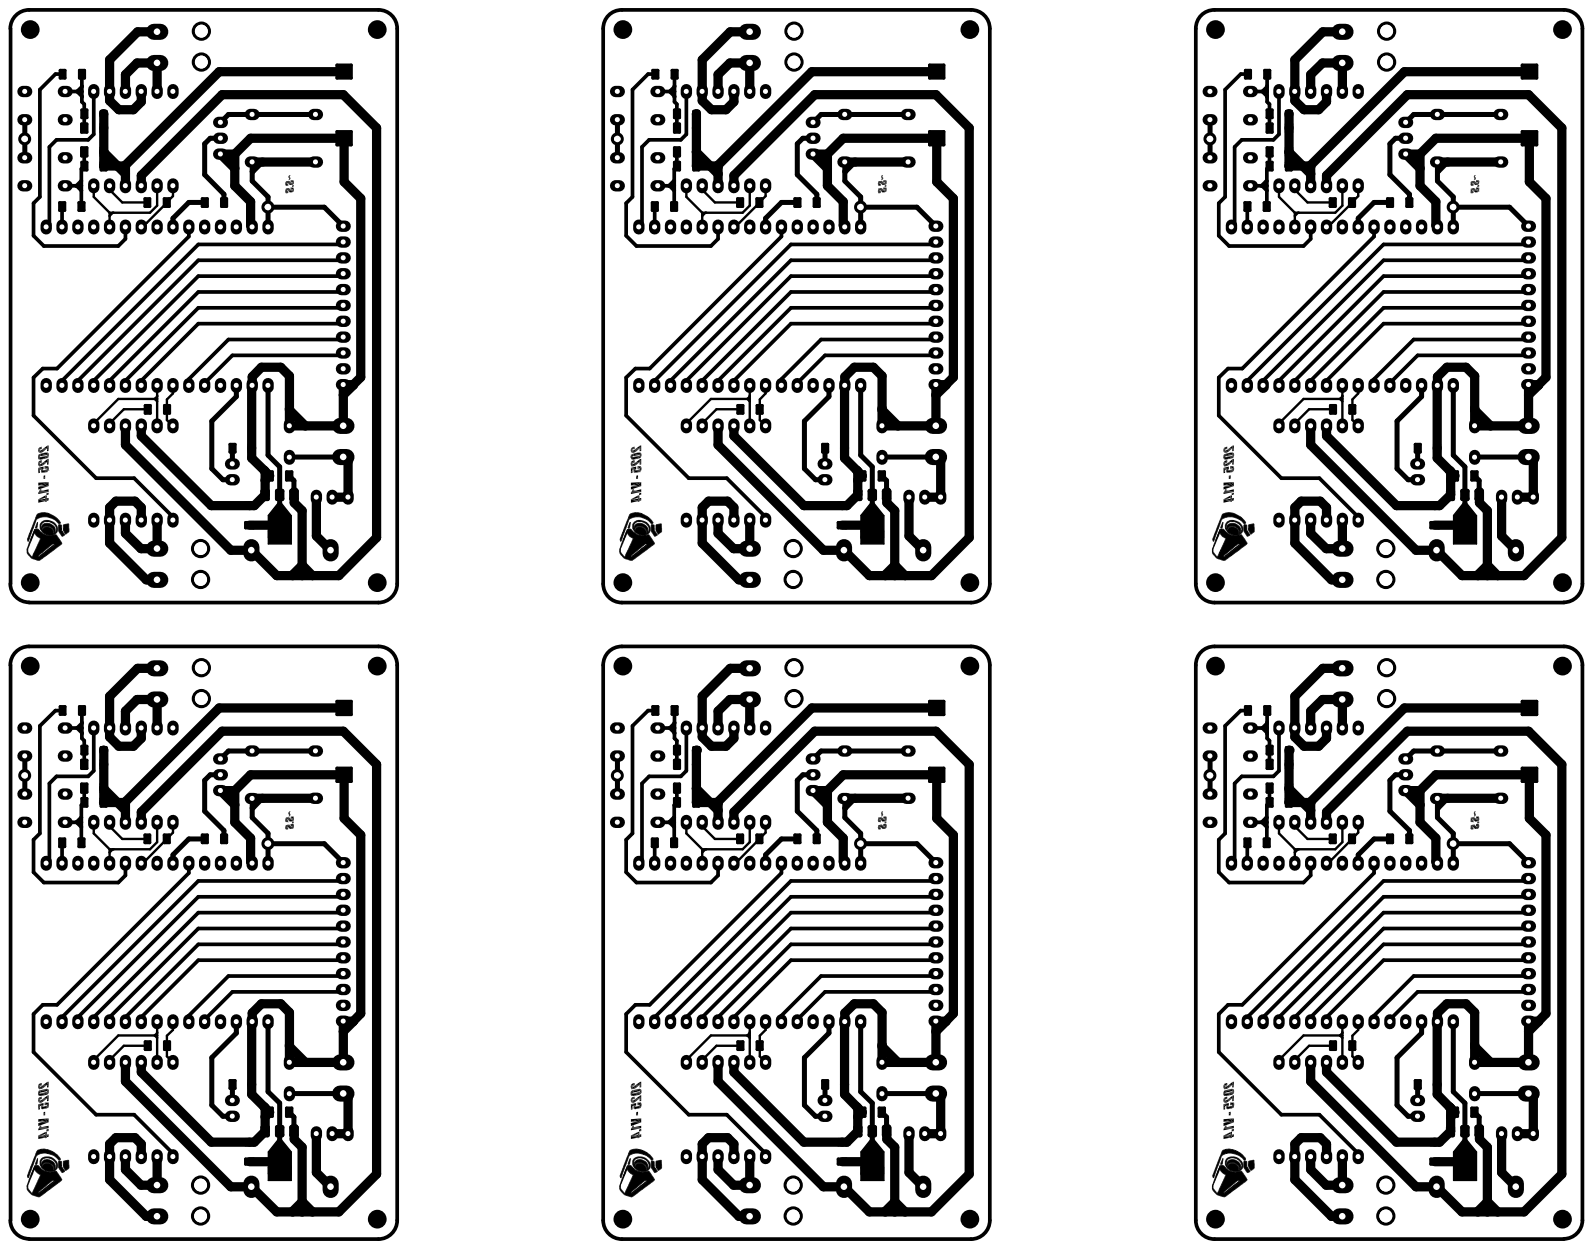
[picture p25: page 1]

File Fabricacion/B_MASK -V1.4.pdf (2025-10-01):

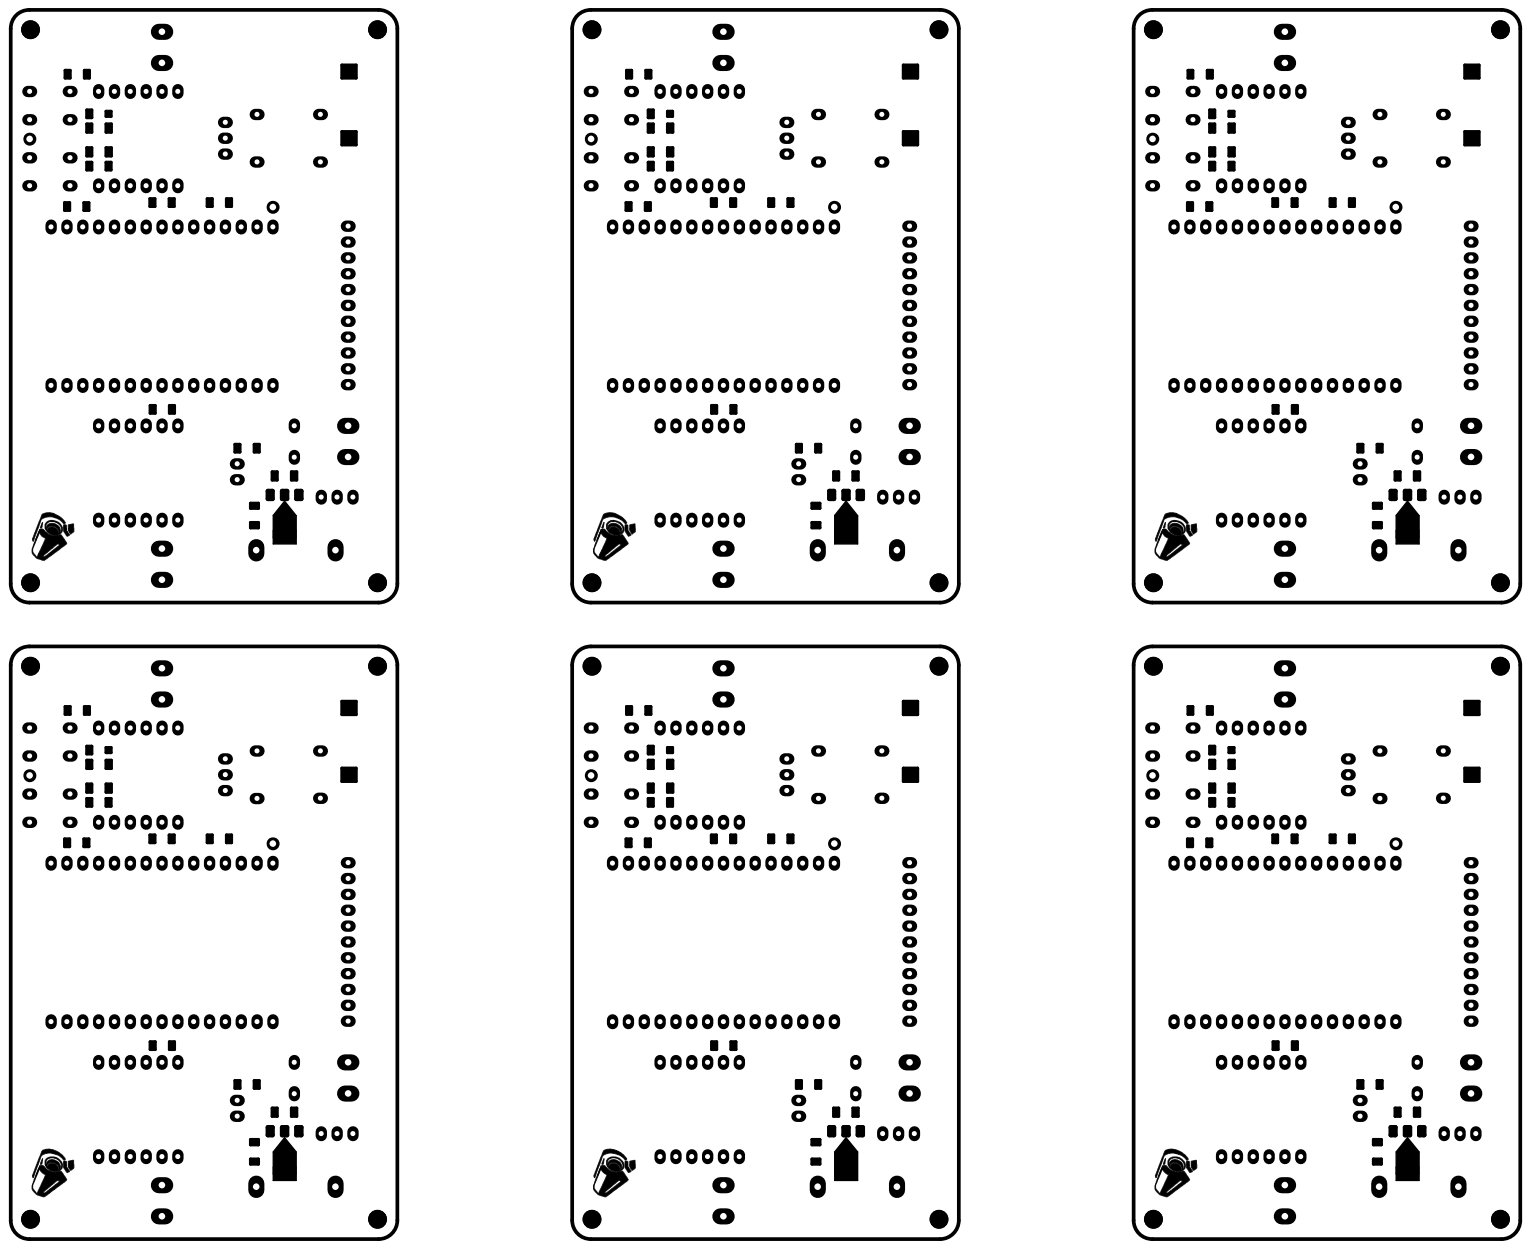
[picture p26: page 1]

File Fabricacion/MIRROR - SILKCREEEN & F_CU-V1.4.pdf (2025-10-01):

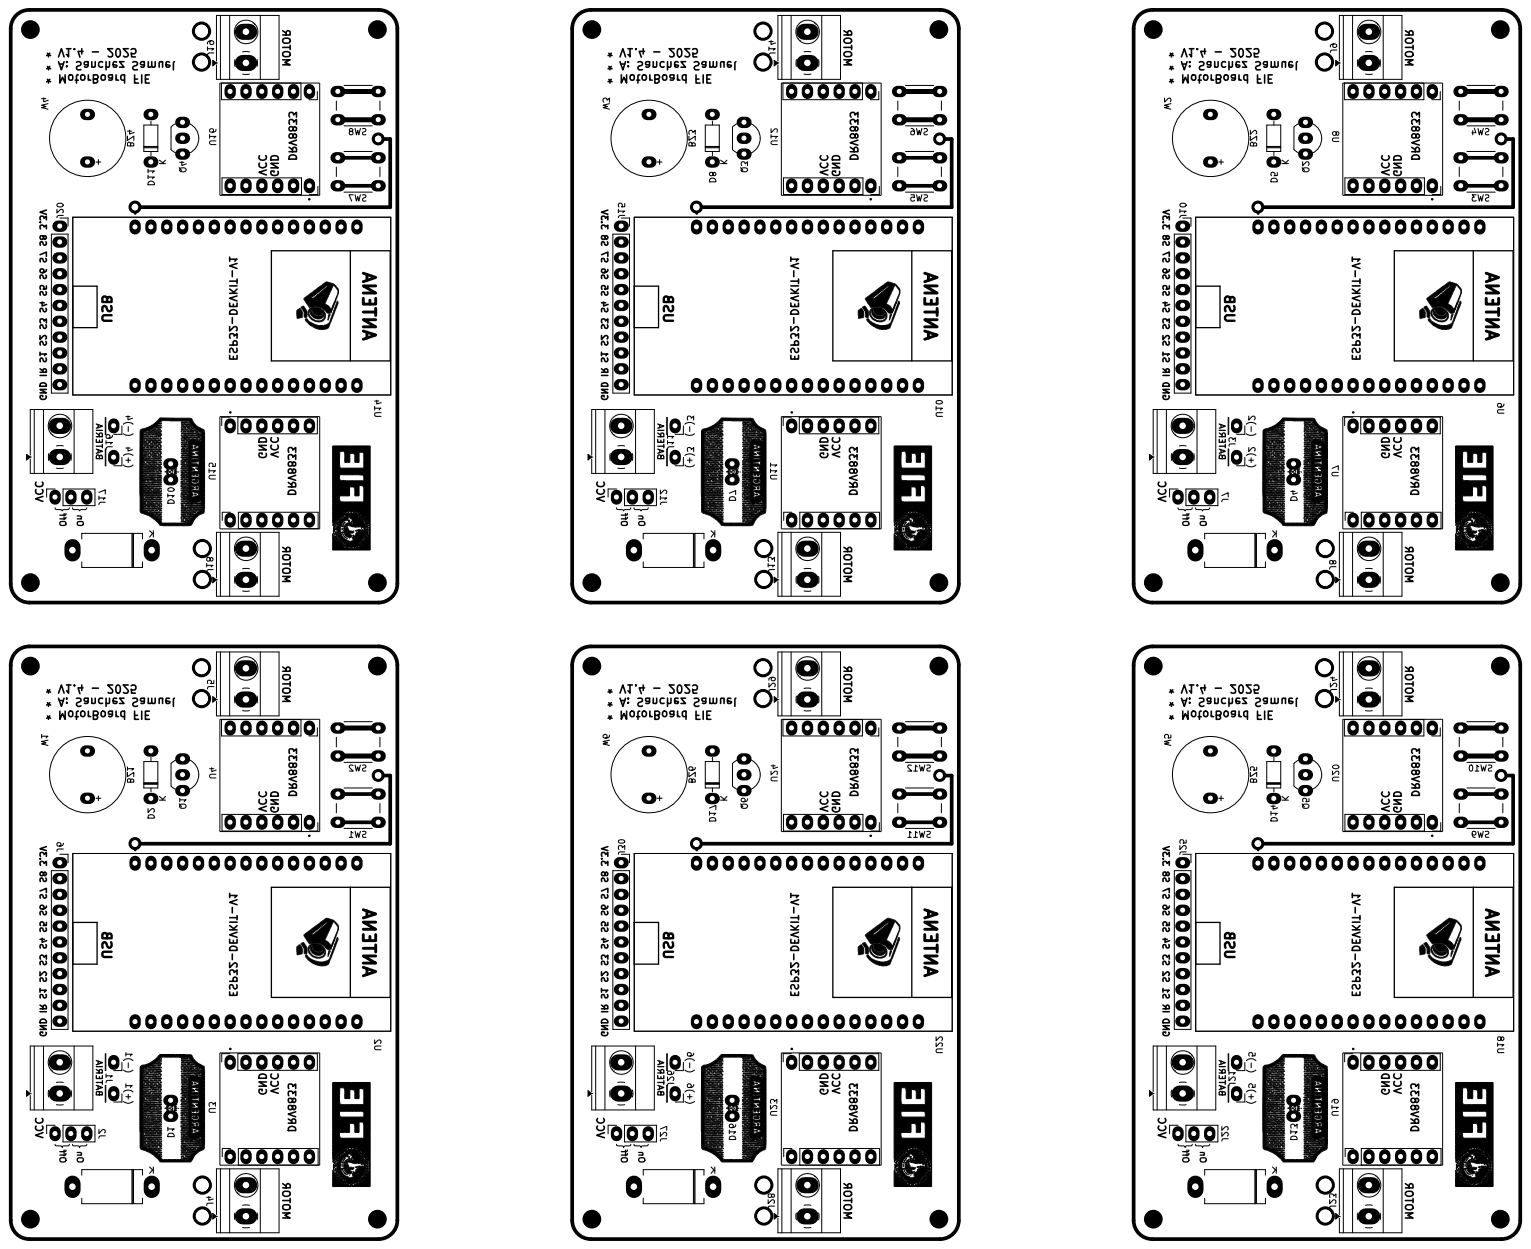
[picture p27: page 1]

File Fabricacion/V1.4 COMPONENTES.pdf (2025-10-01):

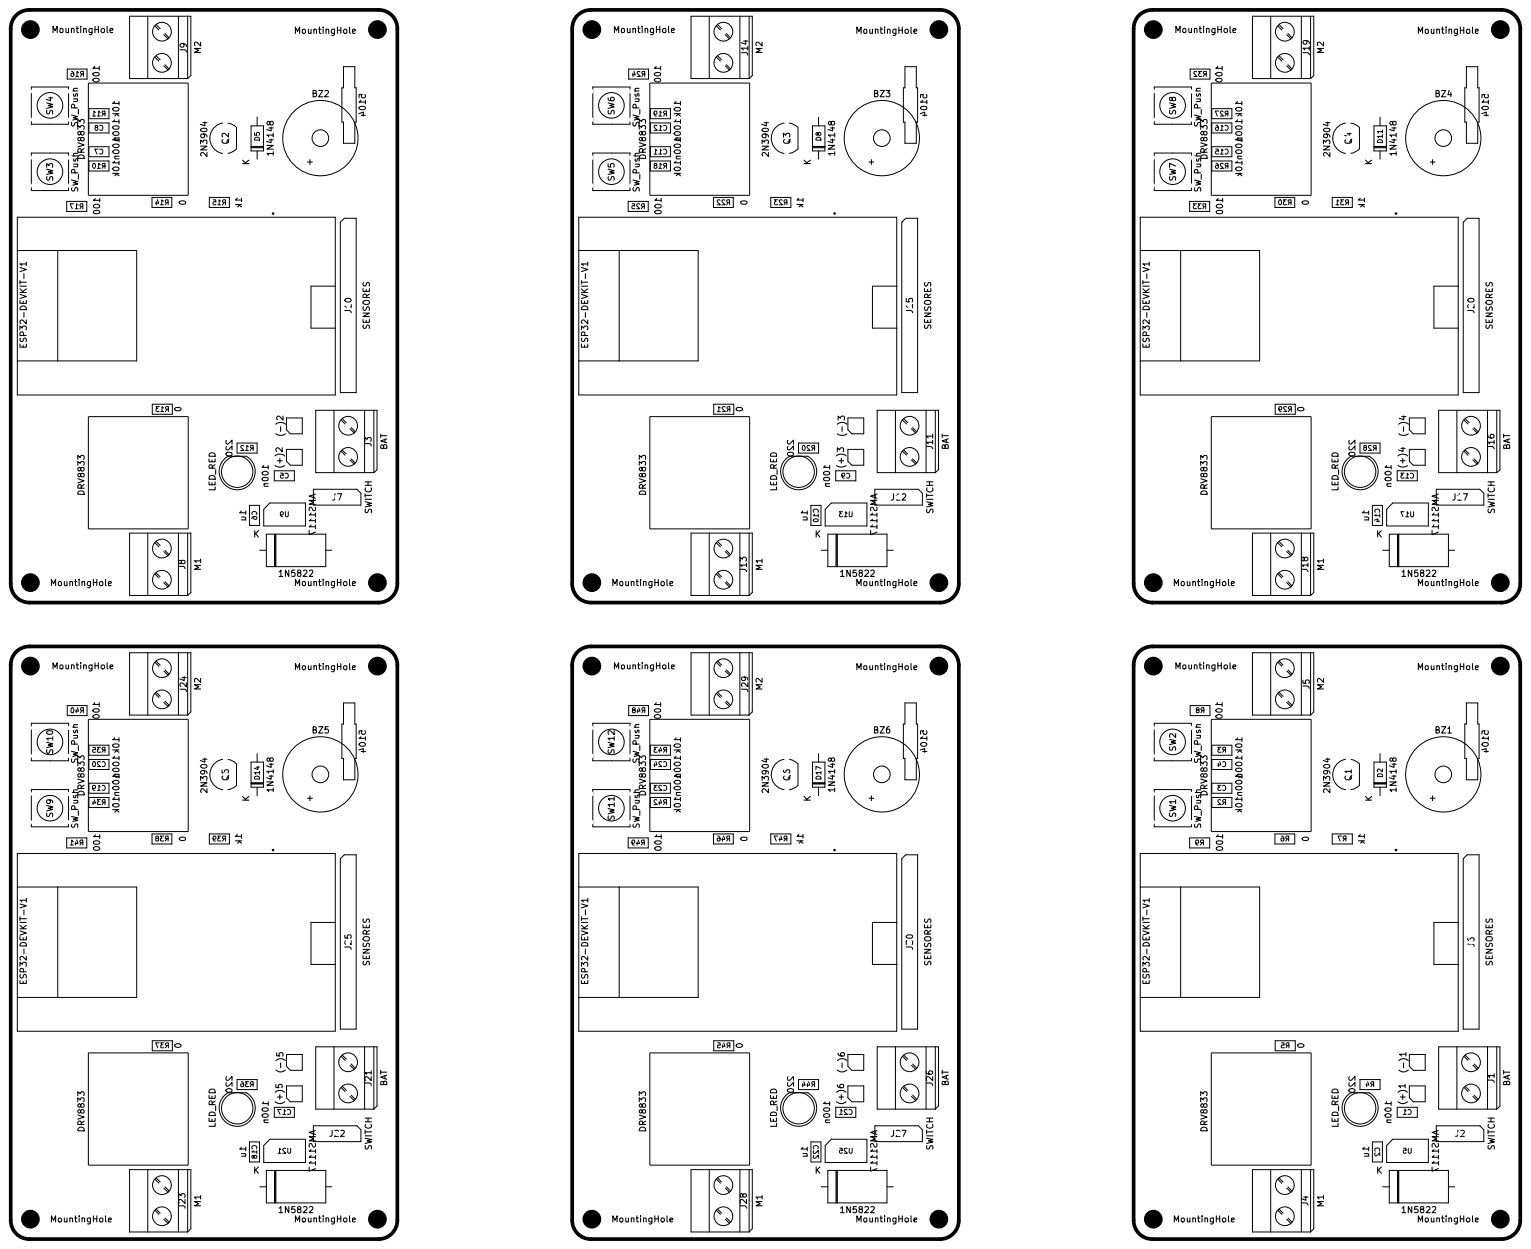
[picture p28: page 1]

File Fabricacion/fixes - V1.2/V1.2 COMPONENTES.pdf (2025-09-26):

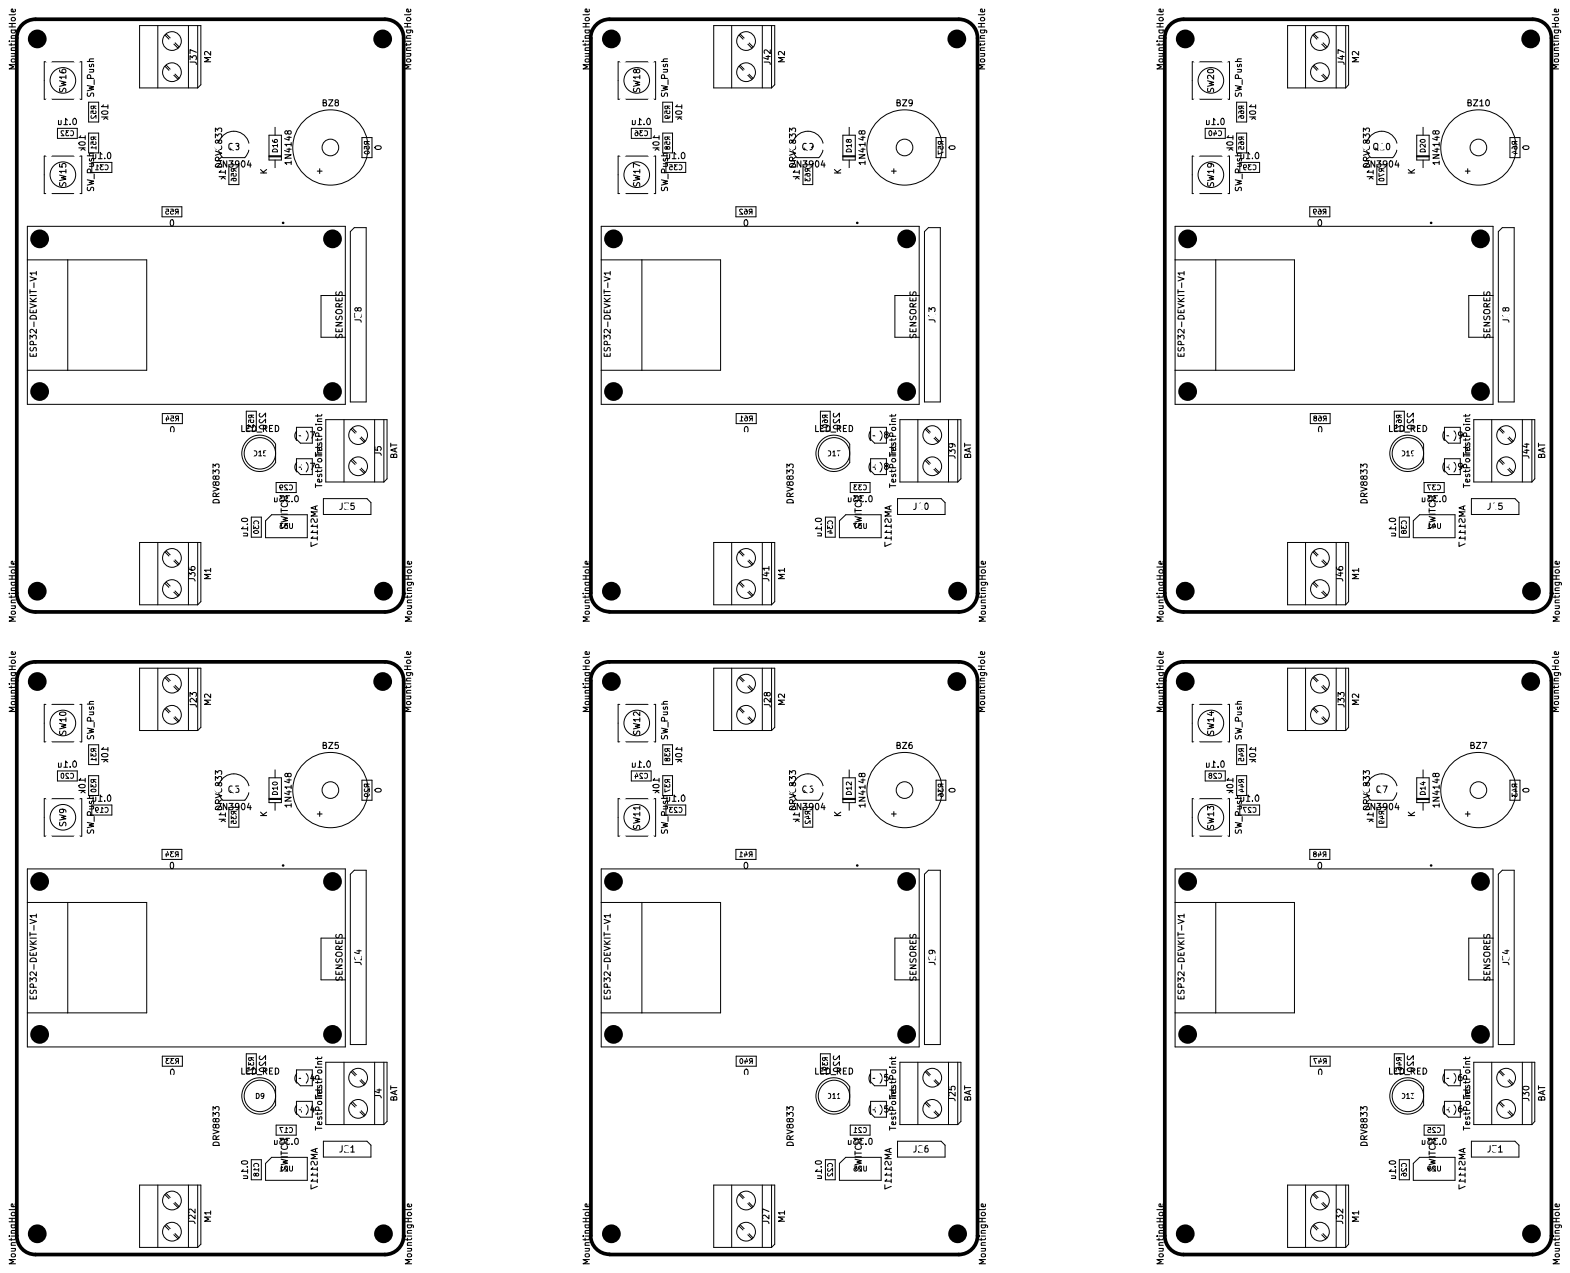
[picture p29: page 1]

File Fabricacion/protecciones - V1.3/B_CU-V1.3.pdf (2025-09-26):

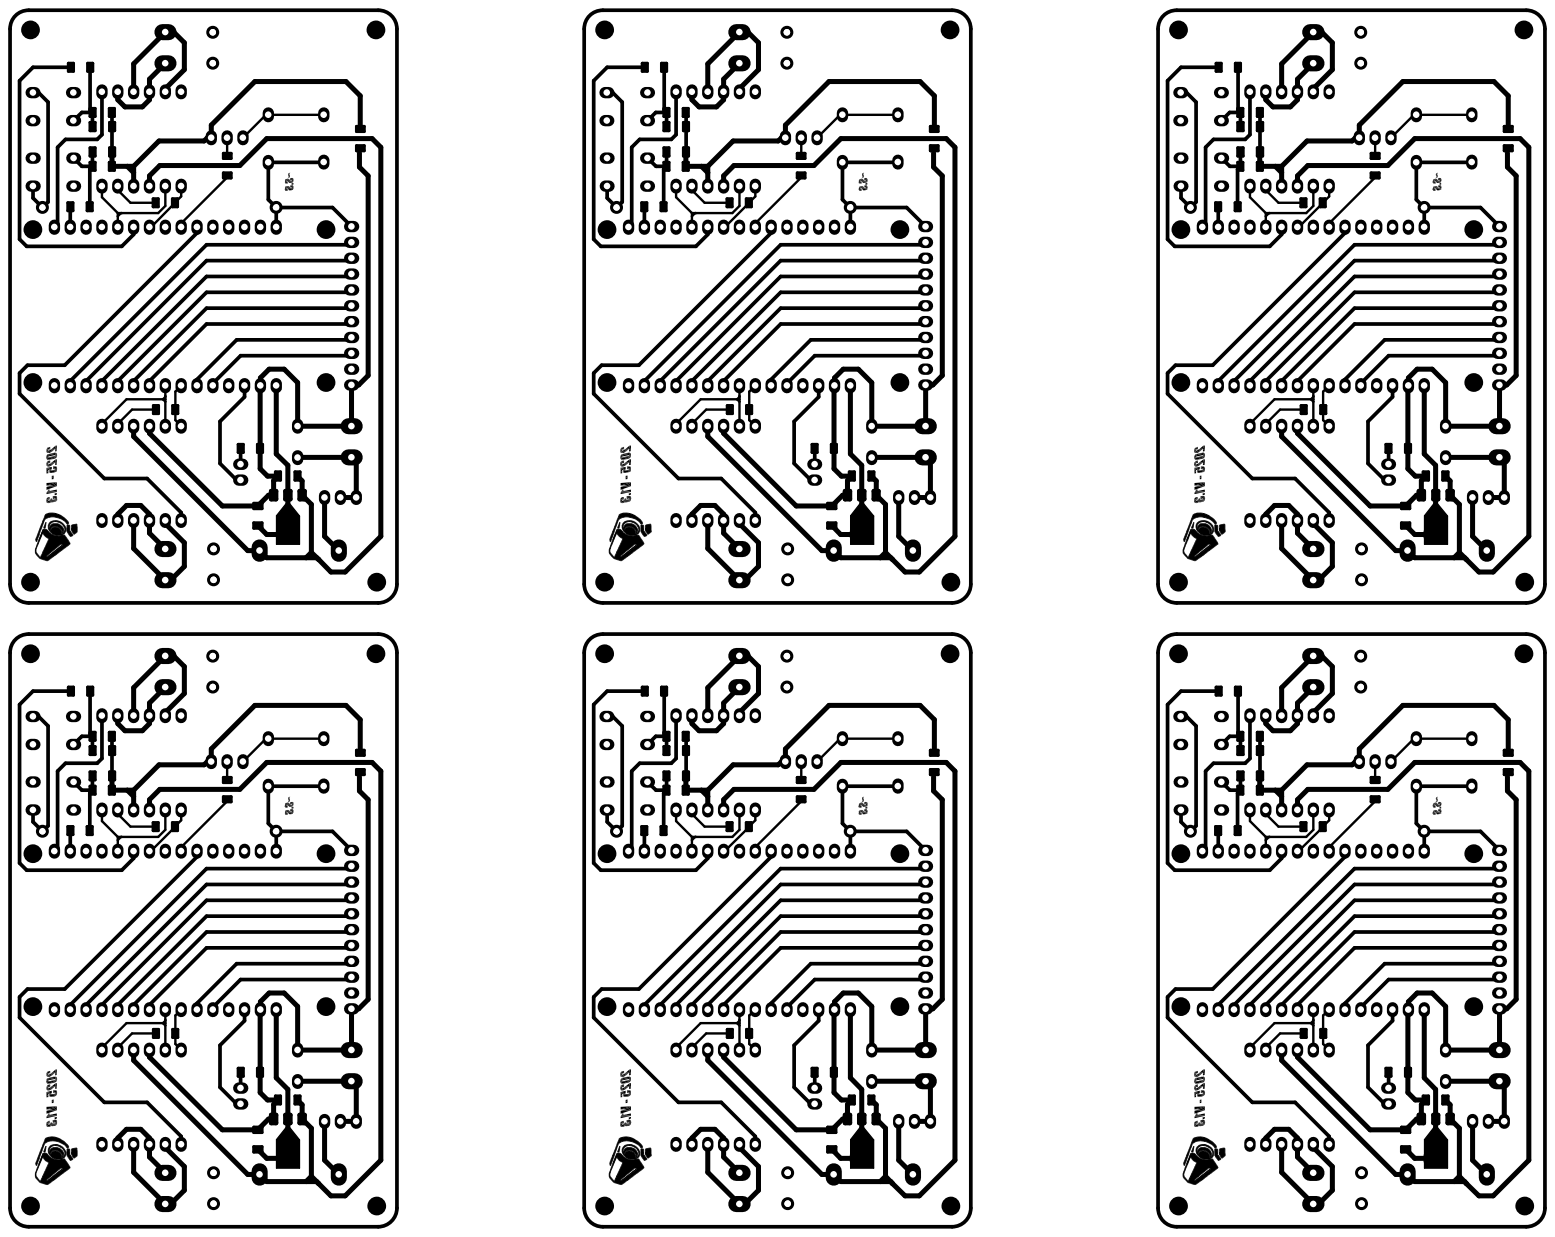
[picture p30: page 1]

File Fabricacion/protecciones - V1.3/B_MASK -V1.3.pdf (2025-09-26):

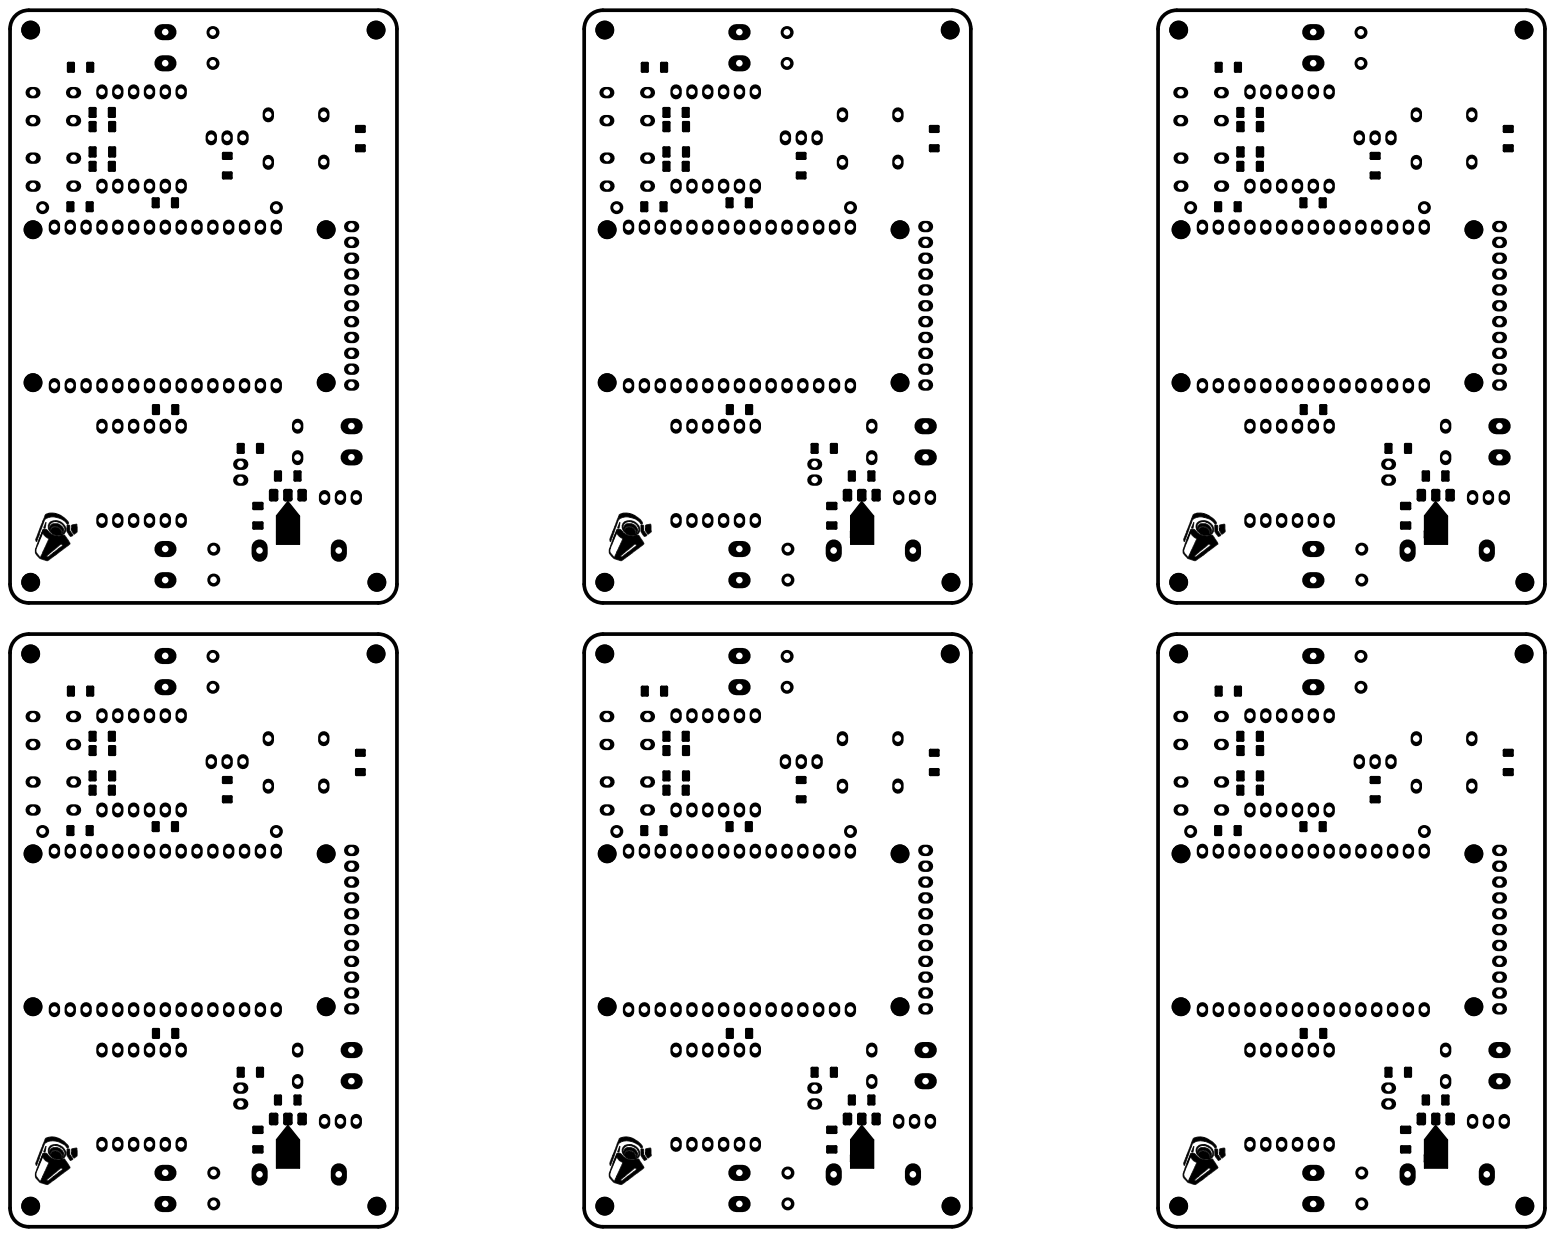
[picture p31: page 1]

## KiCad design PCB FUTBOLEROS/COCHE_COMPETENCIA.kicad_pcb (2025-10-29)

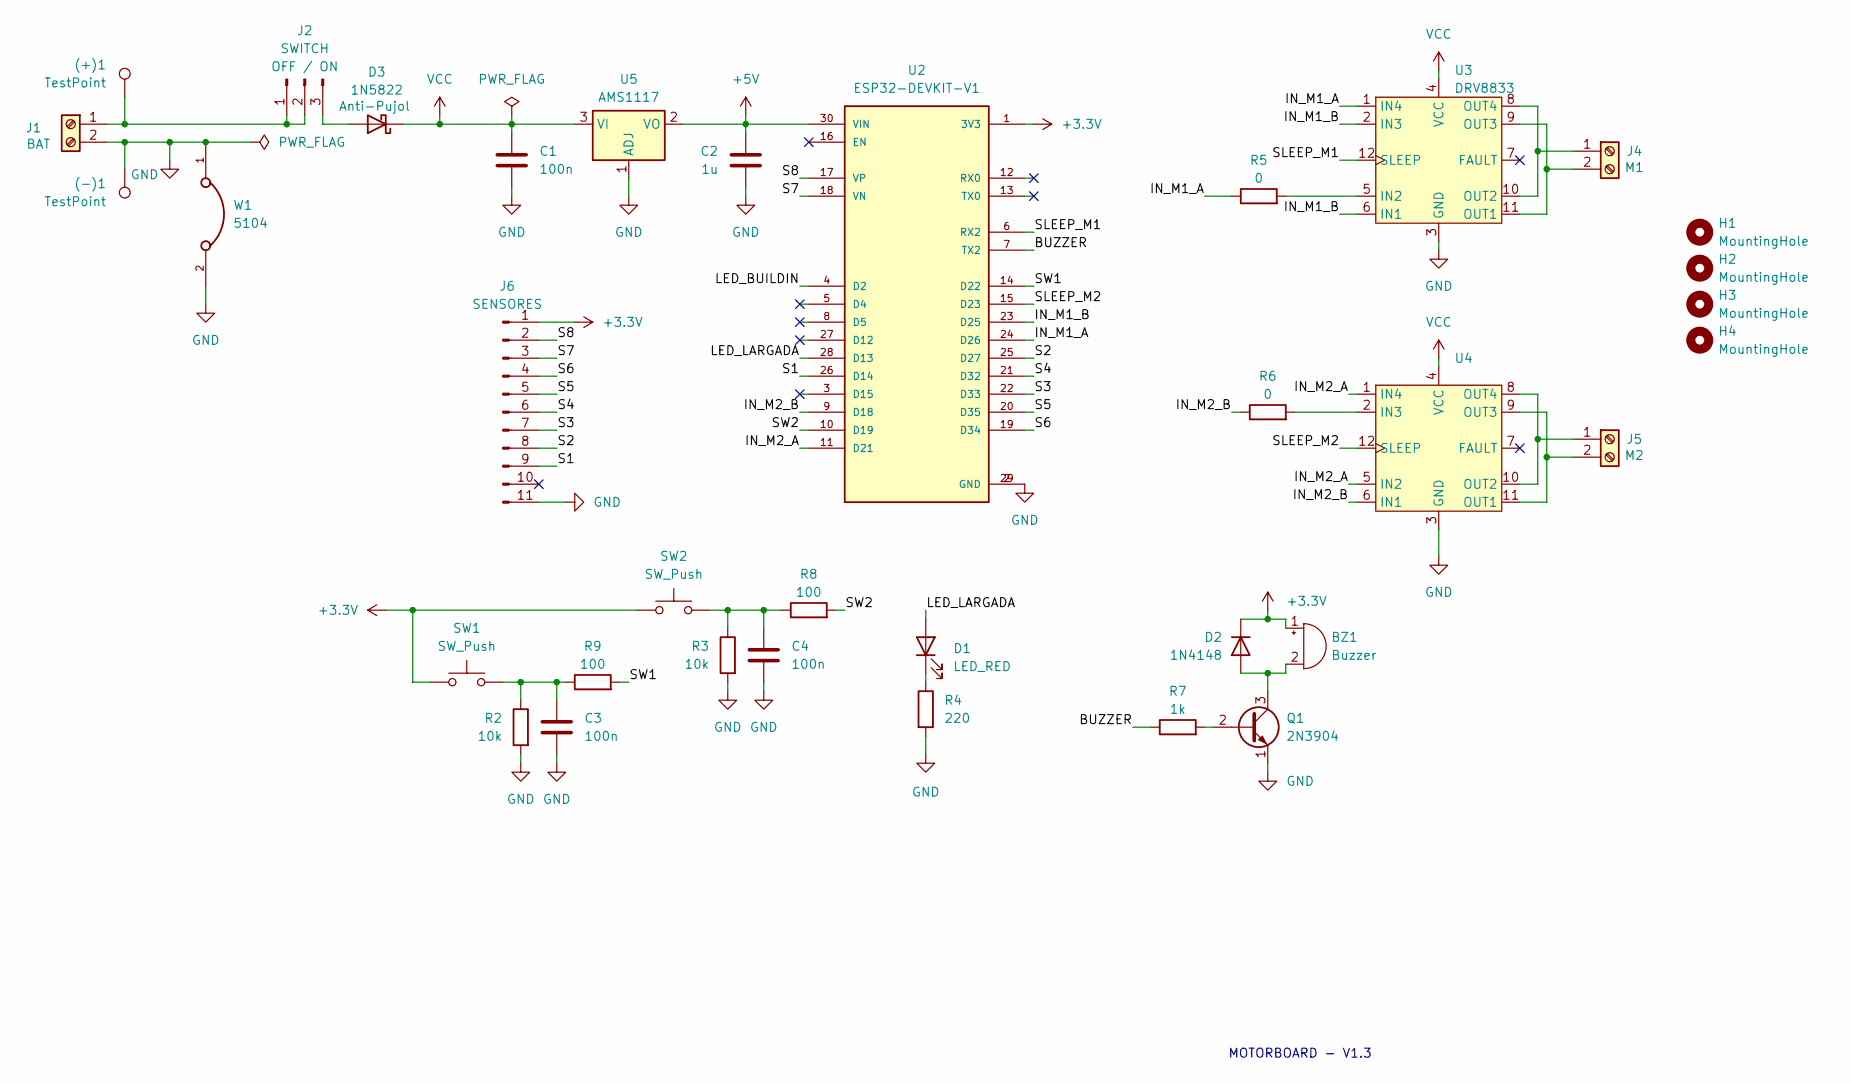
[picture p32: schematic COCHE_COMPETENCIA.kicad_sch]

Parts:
(+)1: TestPoint; PinHeader_1x01_P2.54mm_Vertical
(-)1: TestPoint; PinHeader_1x01_P2.54mm_Vertical
BZ1: Buzzer; MagneticBuzzer_ProSignal_ABI-009-RC
C1, C3, C4: 100n; C_1206_3216Metric_Pad1.33x1.80mm_HandSolder
C2: 1u; C_1206_3216Metric_Pad1.33x1.80mm_HandSolder
D1: LED_RED; LED_D5.0mm
D2: 1N4148; D_DO-35_SOD27_P7.62mm_Horizontal
D3: 1N5822; D_DO-201AD_P12.70mm_Horizontal
H1, H2, H3, H4: MountingHole; MountingHole_3mm
J1: BAT; TerminalBlock_Phoenix_MKDS-1,5-2_1x02_P5.00mm_Horizontal
J2: SWITCH; PinHeader_1x03_P2.54mm_Vertical
J4: M1; TerminalBlock_Phoenix_MKDS-1,5-2_1x02_P5.00mm_Horizontal
J5: M2; TerminalBlock_Phoenix_MKDS-1,5-2_1x02_P5.00mm_Horizontal
J6: SENSORES; PinHeader_1x11_P2.54mm_Vertical
Q1: 2N3904; TO-92_Inline_Wide
R2, R3: 10k; R_1206_3216Metric_Pad1.30x1.75mm_HandSolder
R4: 220; R_1206_3216Metric_Pad1.30x1.75mm_HandSolder
R5, R6: 0; R_1206_3216Metric_Pad1.30x1.75mm_HandSolder
R7: 1k; R_1206_3216Metric_Pad1.30x1.75mm_HandSolder
R8, R9: 100; R_1206_3216Metric_Pad1.30x1.75mm_HandSolder
SW1, SW2: SW_Push; SW_PUSH_6mm_H5mm
U2: ESP32-DEVKIT-V1; MODULE_ESP32_DEVKIT_V1; PARTREV N/A
U3, U4: DRV8833
U5: AMS1117; SOT-223-3_TabPin2
W1: 5104; KEYSTONE_5104; PARTREV A

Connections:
+3.3V: BZ1.1 (+), D2.1 (K), J6.1, SW1.1, SW2.1, U2.1 (3V3)
+5V: C2.1, U2.30 (VIN), U5.2 (VO)
/BUZZER: R7.1, U2.7 (TX2)
/IN_M1_A: R5.1, U2.24 (D26), U3.1 (IN4)
/IN_M1_B: U2.23 (D25), U3.2 (IN3), U3.6 (IN1)
/IN_M2_A: U2.11 (D21), U4.1 (IN4), U4.5 (IN2)
/IN_M2_B: R6.1, U2.9 (D18), U4.6 (IN1)
/LED_LARGADA: D1.2 (A), U2.28 (D13)
/S1: J6.9, U2.26 (D14)
/S2: J6.8, U2.25 (D27)
/S3: J6.7, U2.22 (D33)
/S4: J6.6, U2.21 (D32)
/S5: J6.5, U2.20 (D35)
/S6: J6.4, U2.19 (D34)
/S7: J6.3, U2.18 (VN)
/S8: J6.2, U2.17 (VP)
/SLEEP_M1: U2.6 (RX2), U3.12 (SLEEP)
/SLEEP_M2: U2.15 (D23), U4.12 (SLEEP)
/SW1: R9.2, U2.14 (D22)
/SW2: R8.2, U2.10 (D19)
GND: (-)1.1, C1.2, C2.2, C3.2, C4.2, J1.2, J6.11, Q1.1 (E), R2.2, R3.2, R4.2, U2.2 (GND), U2.29 (GND), U3.3 (GND), U4.3 (GND), U5.1 (ADJ), W1.1, W1.2
unnamed: BZ1.2 (-), D2.2 (A), Q1.3 (C)
unnamed: C3.1, R2.1, R9.1, SW1.2
unnamed: C4.1, R3.1, R8.1, SW2.2
unnamed: D1.1 (K), R4.1
unnamed: D3.2 (A), J2.3
unnamed: (+)1.1, J1.1, J2.1, J2.2
unnamed: J4.1, U3.8 (OUT4), U3.10 (OUT2)
unnamed: J4.2, U3.9 (OUT3), U3.11 (OUT1)
unnamed: J5.1, U4.8 (OUT4), U4.10 (OUT2)
unnamed: J5.2, U4.9 (OUT3), U4.11 (OUT1)
unnamed: Q1.2 (B), R7.2
unnamed: R5.2, U3.5 (IN2)
unnamed: R6.2, U4.2 (IN3)
VCC: C1.1, D3.1 (K), U3.4 (VCC), U4.4 (VCC), U5.3 (VI)

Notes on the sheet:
MOTORBOARD - V1.3

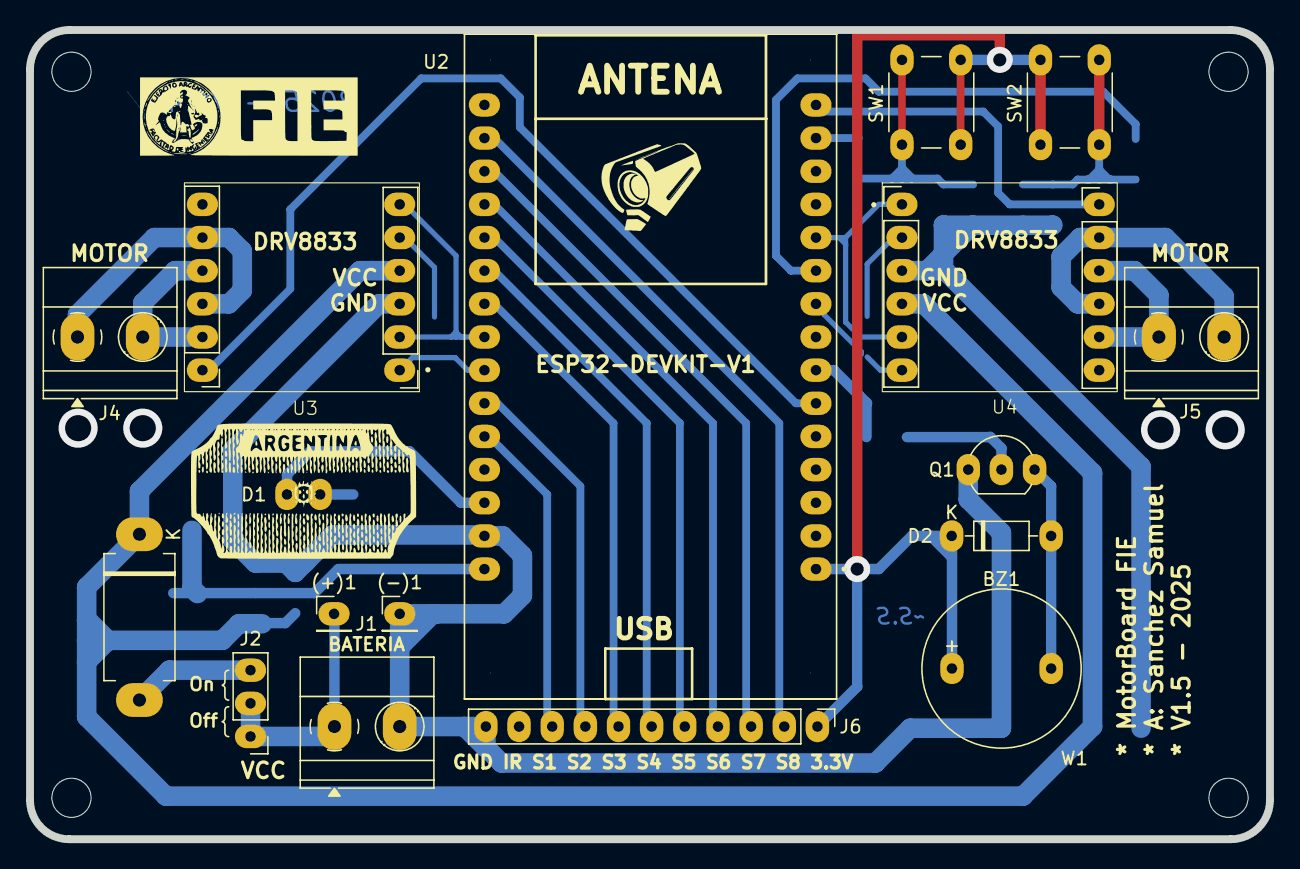
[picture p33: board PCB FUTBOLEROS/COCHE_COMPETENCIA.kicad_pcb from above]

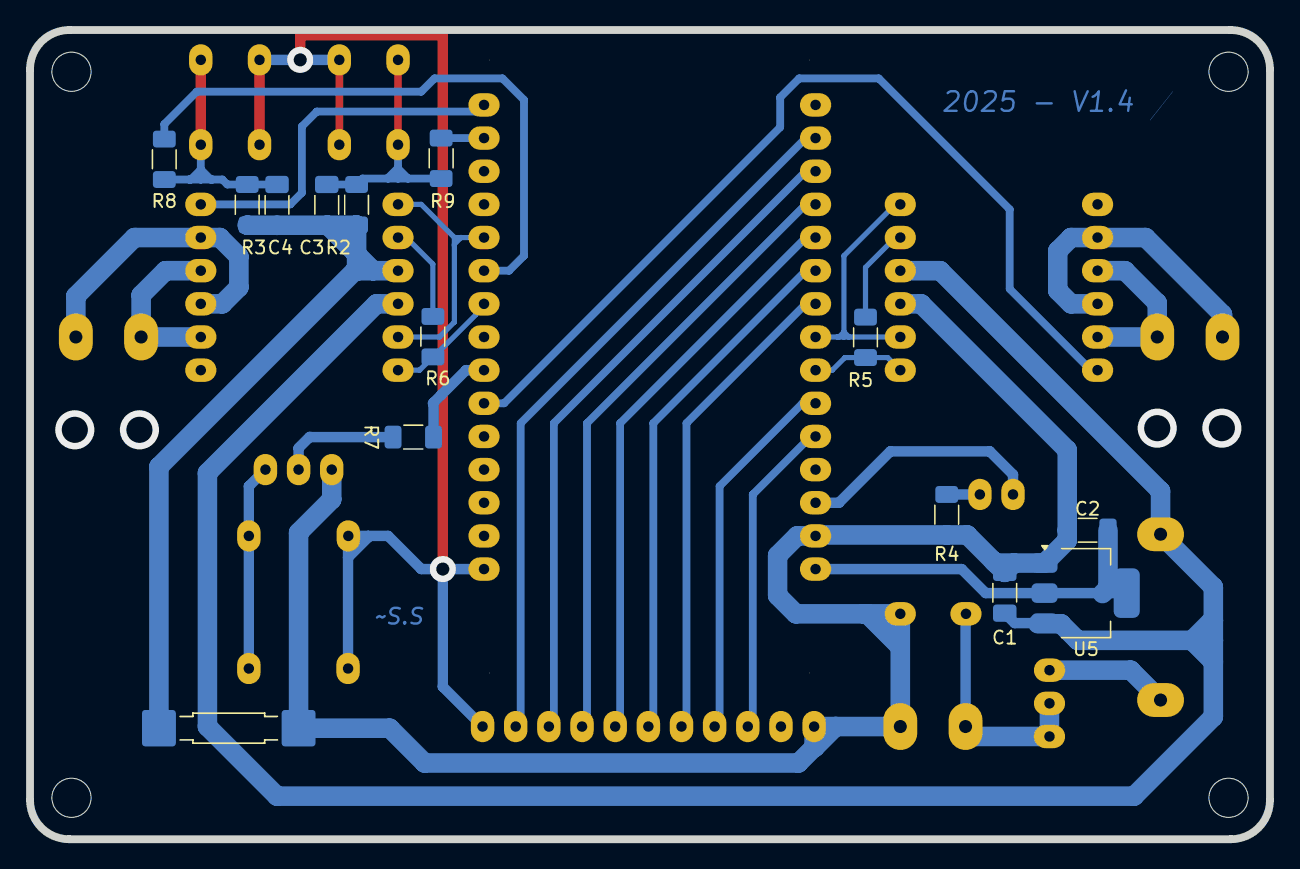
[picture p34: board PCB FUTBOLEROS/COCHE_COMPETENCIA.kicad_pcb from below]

Board: 2 copper layers, 95.0 x 62.0 mm, 35 parts (14 on the bottom side), 35 nets.

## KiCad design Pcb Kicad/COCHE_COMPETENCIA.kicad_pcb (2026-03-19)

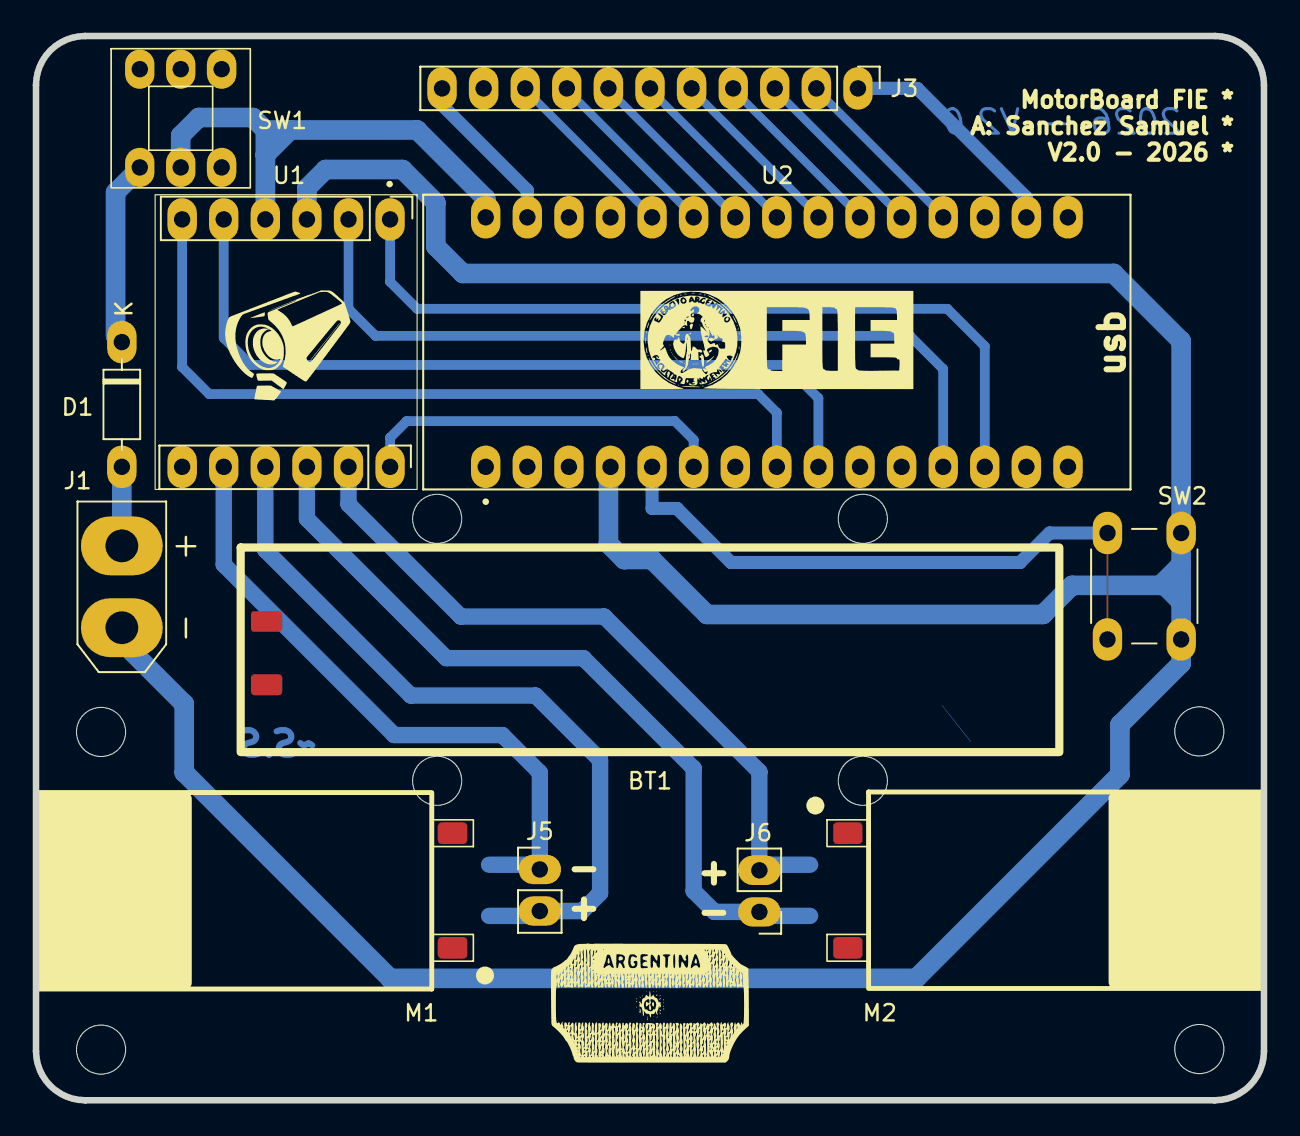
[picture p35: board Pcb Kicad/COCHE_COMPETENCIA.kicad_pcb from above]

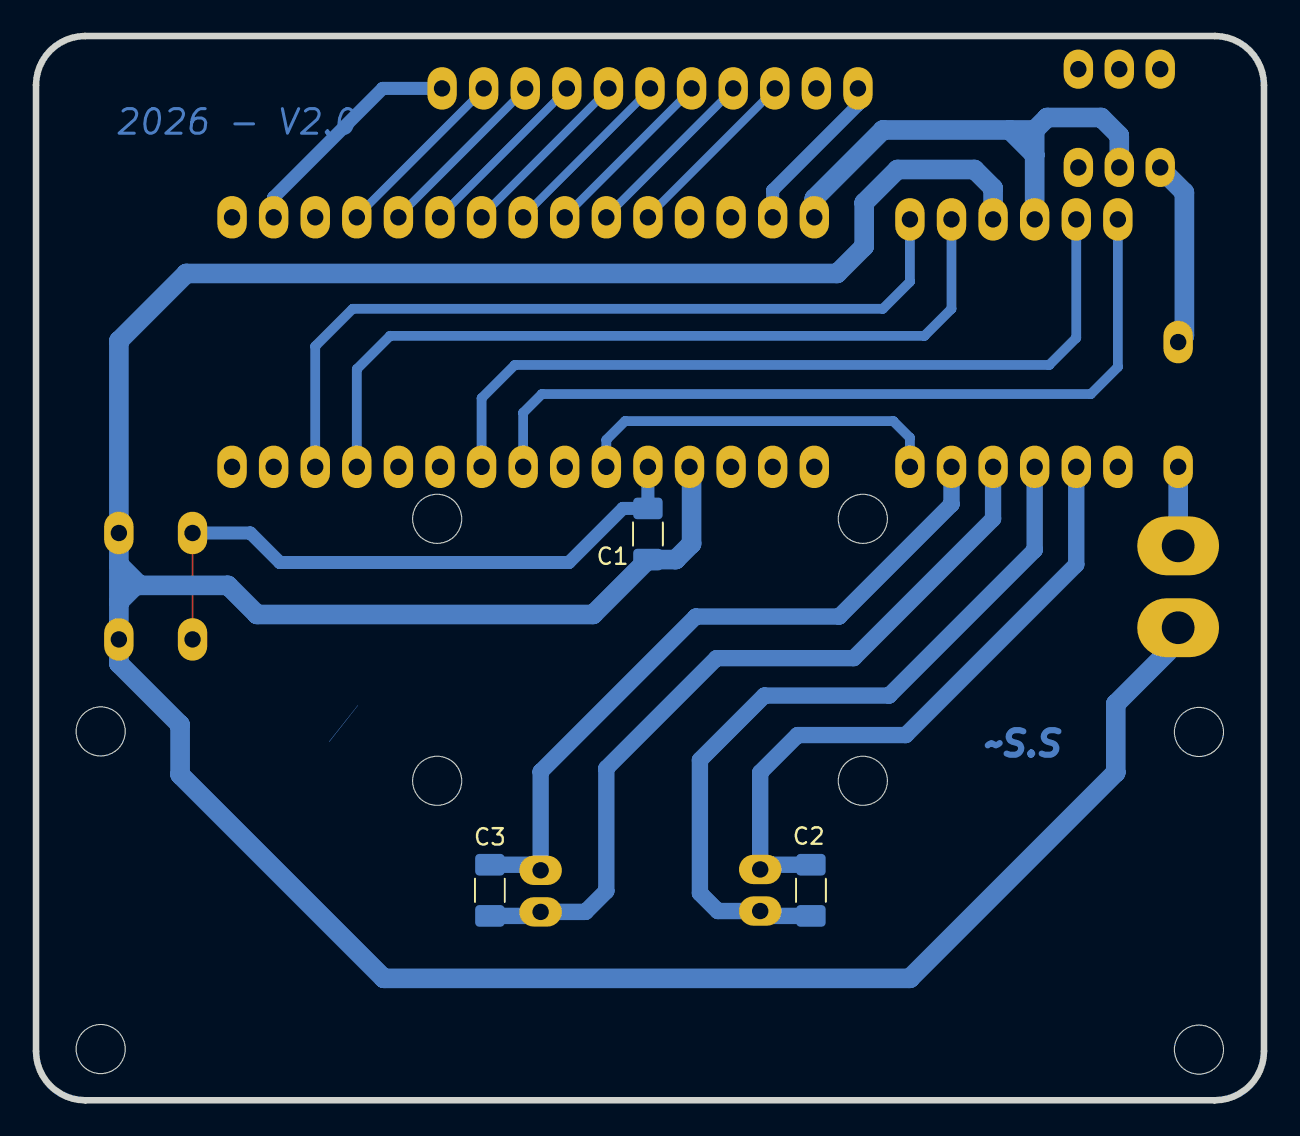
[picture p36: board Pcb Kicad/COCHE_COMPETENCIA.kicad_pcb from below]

Board: 2 copper layers, 75.0 x 65.0 mm, 15 parts (3 on the bottom side), 24 nets.

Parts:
BT1: 2S 70C 250mAH; Bateria_Lado
C1, C2, C3: 100n; C_1206_3216Metric_Pad1.33x1.80mm_HandSolder
D1: D_Schottky; D_DO-35_SOD27_P7.62mm_Horizontal
J1: BAT; AMASS_XT30UPB-M_1x02_P5.0mm_Vertical
J3: SENSORES; PinHeader_1x11_P2.54mm_Vertical
J5: M1; PinHeader_1x02_P2.54mm_Vertical
J6: M2; PinHeader_1x02_P2.54mm_Vertical
M1, M2: Pololu DC; pololu
SW1: ON/OFF; SWITCH_6PINS
SW2: SW_RUN; SW_PUSH_6mm_H5mm
U1: DRV8833
U2: ARDUINO_NANO; MODULE_ARDUINO_NANO

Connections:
+3.3V: J3.1, U2.17 (3V3)
/BAT+: D1.2 (A), J1.2
/IN_M1_A: U1.1 (IN4), U2.13 (D10)
/IN_M1_B: U1.2 (IN3), U2.12 (D9)
/IN_M2_A: U1.5 (IN2), U2.9 (D6)
/IN_M2_B: U1.6 (IN1), U2.8 (D5)
/OUT1+: C2.2, J5.2, U1.9 (OUT3)
/OUT1-: C2.1, J5.1, U1.8 (OUT4)
/OUT2+: C3.1, J6.2, U1.11 (OUT1)
/OUT2-: C3.2, J6.1, U1.10 (OUT2)
/S1: J3.9, U2.26 (A7)
/S2: J3.8, U2.25 (A6)
/S3: J3.7, U2.24 (A5)
/S4: J3.6, U2.23 (A4)
/S5: J3.5, U2.22 (A3)
/S6: J3.4, U2.21 (A2)
/S7: J3.3, U2.20 (A1)
/S8: J3.2, U2.19 (A0)
/SLEEP: U1.12 (SLEEP), U2.6 (D3)
/SW1: C1.1, SW2.1, U2.5 (D2)
GND: J3.11, U2.29 (GND_29)
GND_BAT: C1.2, J1.1, SW2.2, U1.3 (GND), U2.4 (GND_4)
unnamed: D1.1 (K), SW1.3 (B)
VCC: SW1.2 (C), U1.4 (VCC), U2.30 (VIN)

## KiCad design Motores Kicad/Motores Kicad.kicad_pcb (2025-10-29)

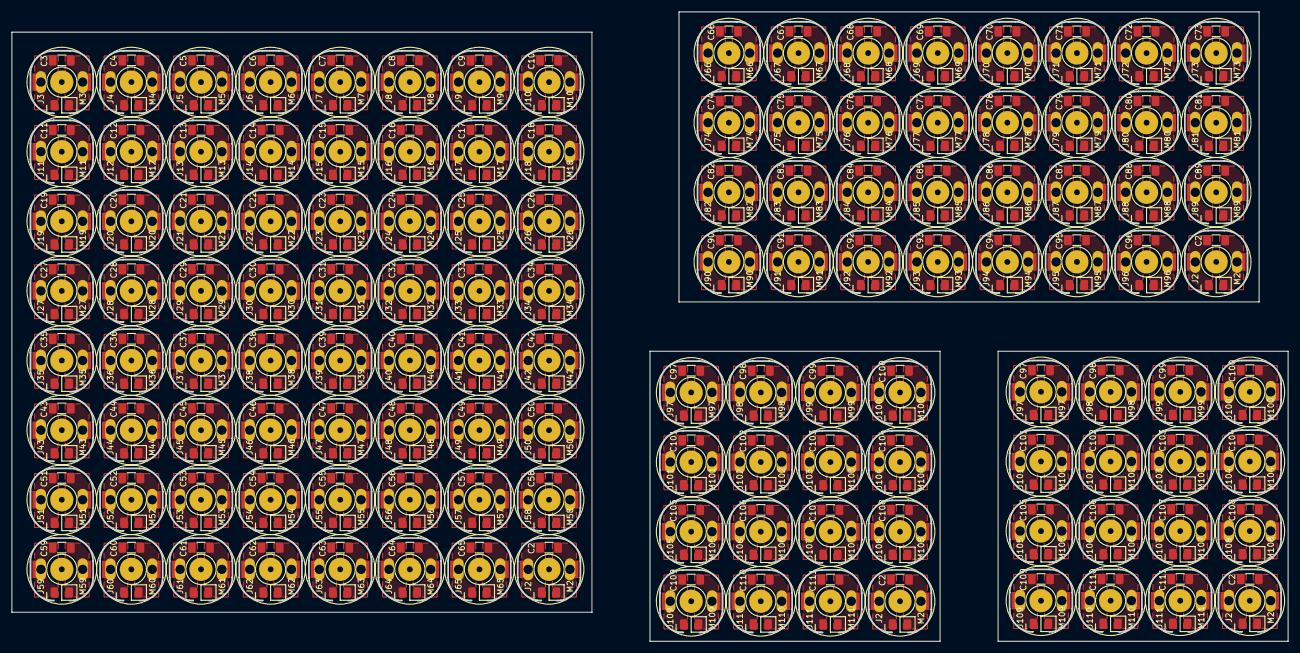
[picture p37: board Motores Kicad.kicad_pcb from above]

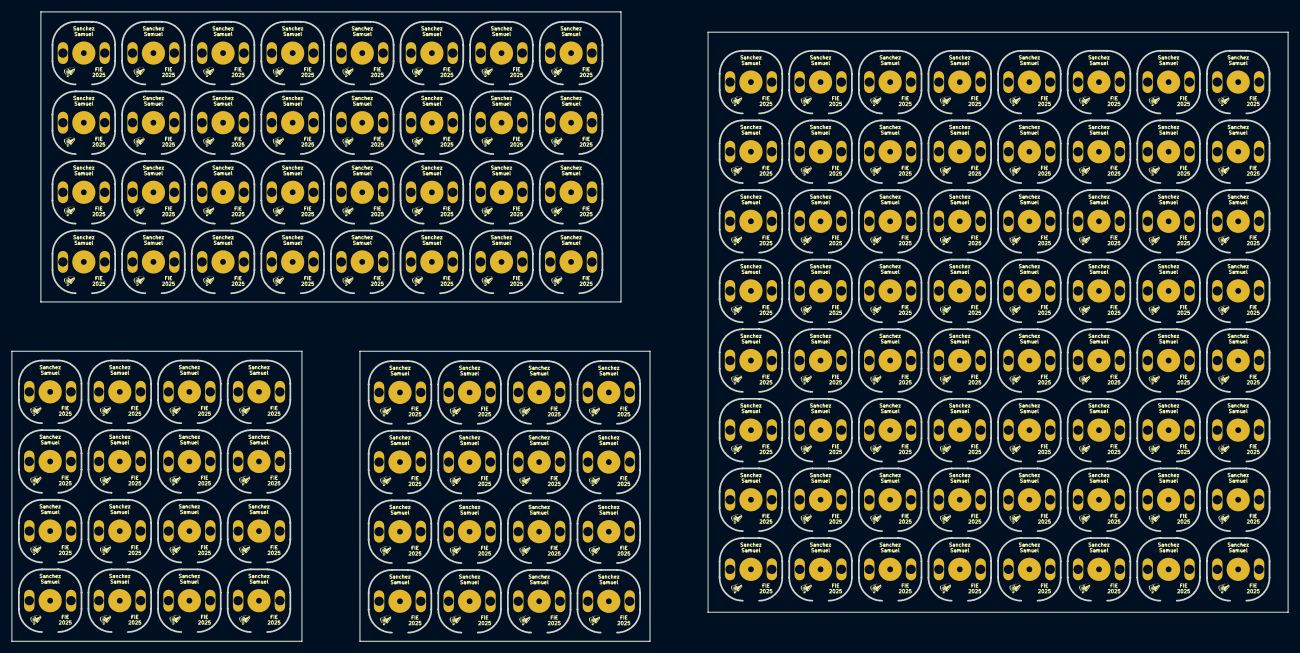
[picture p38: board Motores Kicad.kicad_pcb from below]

Board: 2 copper layers, 220.0 x 108.5 mm, 512 parts (128 on the bottom side), 2 nets, no tracks yet.

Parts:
C2, C2#2, C2#3, C2#4, C3, C4, C5, C6, C7, C8, C9, C10, C11, C12, C13, C14, C15, C16, C17, C18, C19, C20, C21, C22, C23, C24, C25, C26, C27, C28, C29, C30, C31, C32, C33, C34, C35, C36, C37, C38, C39, C40, C41, C42, C43, C44, C45, C46, C47, C48, C49, C50, C51, C52, C53, C54, C55, C56, C57, C58, C59, C60, C61, C62, C63, C64, C65, C66, C67, C68, C69, C70, C71, C72, C73, C74, C75, C76, C77, C78, C79, C80, C81, C82, C83, C84, C85, C86, C87, C88, C89, C90, C91, C92, C93, C94, C95, C96, C97, C97#2, C98, C98#2, C99, C99#2, C100, C100#2, C101, C101#2, C102, C102#2, C103, C103#2, C104, C104#2, C105, C105#2, C106, C106#2, C107, C107#2, C108, C108#2, C109, C109#2, C110, C110#2, C111, C111#2: 3.3nF; C_1206_3216Metric_Pad1.33x1.80mm_HandSolder
J2, J2#2, J2#3, J2#4, J3, J4, J5, J6, J7, J8, J9, J10, J11, J12, J13, J14, J15, J16, J17, J18, J19, J20, J21, J22, J23, J24, J25, J26, J27, J28, J29, J30, J31, J32, J33, J34, J35, J36, J37, J38, J39, J40, J41, J42, J43, J44, J45, J46, J47, J48, J49, J50, J51, J52, J53, J54, J55, J56, J57, J58, J59, J60, J61, J62, J63, J64, J65, J66, J67, J68, J69, J70, J71, J72, J73, J74, J75, J76, J77, J78, J79, J80, J81, J82, J83, J84, J85, J86, J87, J88, J89, J90, J91, J92, J93, J94, J95, J96, J97, J97#2, J98, J98#2, J99, J99#2, J100, J100#2, J101, J101#2, J102, J102#2, J103, J103#2, J104, J104#2, J105, J105#2, J106, J106#2, J107, J107#2, J108, J108#2, J109, J109#2, J110, J110#2, J111, J111#2: Vertical; PinHeader_1x02_P2.54mm_Vertical
M2, M2#2, M2#3, M2#4, M3, M4, M5, M6, M7, M8, M9, M10, M11, M12, M13, M14, M15, M16, M17, M18, M19, M20, M21, M22, M23, M24, M25, M26, M27, M28, M29, M30, M31, M32, M33, M34, M35, M36, M37, M38, M39, M40, M41, M42, M43, M44, M45, M46, M47, M48, M49, M50, M51, M52, M53, M54, M55, M56, M57, M58, M59, M60, M61, M62, M63, M64, M65, M66, M67, M68, M69, M70, M71, M72, M73, M74, M75, M76, M77, M78, M79, M80, M81, M82, M83, M84, M85, M86, M87, M88, M89, M90, M91, M92, M93, M94, M95, M96, M97, M97#2, M98, M98#2, M99, M99#2, M100, M100#2, M101, M101#2, M102, M102#2, M103, M103#2, M104, M104#2, M105, M105#2, M106, M106#2, M107, M107#2, M108, M108#2, M109, M109#2, M110, M110#2, M111, M111#2: Pololu
V4, V4#2, V4#3, V4#4, V5, V6, V7, V8, V9, V10, V11, V12, V13, V14, V15, V16, V17, V18, V19, V20, V21, V22, V23, V24, V25, V26, V27, V28, V29, V30, V31, V32, V33, V34, V35, V36, V37, V38, V39, V40, V41, V42, V43, V44, V45, V46, V47, V48, V49, V50, V51, V52, V53, V54, V55, V56, V57, V58, V59, V60, V61, V62, V63, V64, V65, V66, V67, V68, V69, V70, V71, V72, V73, V74, V75, V76, V77, V78, V79, V80, V81, V82, V83, V84, V85, V86, V87, V88, V89, V90, V91, V92, V93, V94, V95, V96, V97, V98, V99, V99#2, V100, V100#2, V101, V101#2, V102, V102#2, V103, V103#2, V104, V104#2, V105, V105#2, V106, V106#2, V107, V107#2, V108, V108#2, V109, V109#2, V110, V110#2, V111, V111#2, V112, V112#2, V113, V113#2: LOGO

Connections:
/(+): C2.1, C2#2.1, C2#3.1, C2#4.1, C3.1, C4.1, C5.1, C6.1, C7.1, C8.1, C9.1, C10.1, C11.1, C12.1, C13.1, C14.1, C15.1, C16.1, C17.1, C18.1, C19.1, C20.1, C21.1, C22.1, C23.1, C24.1, C25.1, C26.1, C27.1, C28.1, C29.1, C30.1, C31.1, C32.1, C33.1, C34.1, C35.1, C36.1, C37.1, C38.1, C39.1, C40.1, C41.1, C42.1, C43.1, C44.1, C45.1, C46.1, C47.1, C48.1, C49.1, C50.1, C51.1, C52.1, C53.1, C54.1, C55.1, C56.1, C57.1, C58.1, C59.1, C60.1, C61.1, C62.1, C63.1, C64.1, C65.1, C66.1, C67.1, C68.1, C69.1, C70.1, C71.1, C72.1, C73.1, C74.1, C75.1, C76.1, C77.1, C78.1, C79.1, C80.1, C81.1, C82.1, C83.1, C84.1, C85.1, C86.1, C87.1, C88.1, C89.1, C90.1, C91.1, C92.1, C93.1, C94.1, C95.1, C96.1, C97.1, C97#2.1, C98.1, C98#2.1, C99.1, C99#2.1, C100.1, C100#2.1, C101.1, C101#2.1, C102.1, C102#2.1, C103.1, C103#2.1, C104.1, C104#2.1, C105.1, C105#2.1, C106.1, C106#2.1, C107.1, C107#2.1, C108.1, C108#2.1, C109.1, C109#2.1, C110.1, C110#2.1, C111.1, C111#2.1, J2.1, J2#2.1, J2#3.1, J2#4.1, J3.1, J4.1, J5.1, J6.1, J7.1, J8.1, J9.1, J10.1, J11.1, J12.1, J13.1, J14.1, J15.1, J16.1, J17.1, J18.1, J19.1, J20.1, J21.1, J22.1, J23.1, J24.1, J25.1, J26.1, J27.1, J28.1, J29.1, J30.1, J31.1, J32.1, J33.1, J34.1, J35.1, J36.1, J37.1, J38.1, J39.1, J40.1, J41.1, J42.1, J43.1, J44.1, J45.1, J46.1, J47.1, J48.1, J49.1, J50.1, J51.1, J52.1, J53.1, J54.1, J55.1, J56.1, J57.1, J58.1, J59.1, J60.1, J61.1, J62.1, J63.1, J64.1, J65.1, J66.1, J67.1, J68.1, J69.1, J70.1, J71.1, J72.1, J73.1, J74.1, J75.1, J76.1, J77.1, J78.1, J79.1, J80.1, J81.1, J82.1, J83.1, J84.1, J85.1, J86.1, J87.1, J88.1, J89.1, J90.1, J91.1, J92.1, J93.1, J94.1, J95.1, J96.1, J97.1, J97#2.1, J98.1, J98#2.1, J99.1, J99#2.1, J100.1, J100#2.1, J101.1, J101#2.1, J102.1, J102#2.1, J103.1, J103#2.1, J104.1, J104#2.1, J105.1, J105#2.1, J106.1, J106#2.1, J107.1, J107#2.1, J108.1, J108#2.1, J109.1, J109#2.1, J110.1, J110#2.1, J111.1, J111#2.1, M2.1 (+), M2#2.1 (+), M2#3.1 (+), M2#4.1 (+), M3.1 (+), M4.1 (+), M5.1 (+), M6.1 (+), M7.1 (+), M8.1 (+), M9.1 (+), M10.1 (+), M11.1 (+), M12.1 (+), M13.1 (+), M14.1 (+), M15.1 (+), M16.1 (+), M17.1 (+), M18.1 (+)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
/(-): C2.2, C2#2.2, C2#3.2, C2#4.2, C3.2, C4.2, C5.2, C6.2, C7.2, C8.2, C9.2, C10.2, C11.2, C12.2, C13.2, C14.2, C15.2, C16.2, C17.2, C18.2, C19.2, C20.2, C21.2, C22.2, C23.2, C24.2, C25.2, C26.2, C27.2, C28.2, C29.2, C30.2, C31.2, C32.2, C33.2, C34.2, C35.2, C36.2, C37.2, C38.2, C39.2, C40.2, C41.2, C42.2, C43.2, C44.2, C45.2, C46.2, C47.2, C48.2, C49.2, C50.2, C51.2, C52.2, C53.2, C54.2, C55.2, C56.2, C57.2, C58.2, C59.2, C60.2, C61.2, C62.2, C63.2, C64.2, C65.2, C66.2, C67.2, C68.2, C69.2, C70.2, C71.2, C72.2, C73.2, C74.2, C75.2, C76.2, C77.2, C78.2, C79.2, C80.2, C81.2, C82.2, C83.2, C84.2, C85.2, C86.2, C87.2, C88.2, C89.2, C90.2, C91.2, C92.2, C93.2, C94.2, C95.2, C96.2, C97.2, C97#2.2, C98.2, C98#2.2, C99.2, C99#2.2, C100.2, C100#2.2, C101.2, C101#2.2, C102.2, C102#2.2, C103.2, C103#2.2, C104.2, C104#2.2, C105.2, C105#2.2, C106.2, C106#2.2, C107.2, C107#2.2, C108.2, C108#2.2, C109.2, C109#2.2, C110.2, C110#2.2, C111.2, C111#2.2, J2.2, J2#2.2, J2#3.2, J2#4.2, J3.2, J4.2, J5.2, J6.2, J7.2, J8.2, J9.2, J10.2, J11.2, J12.2, J13.2, J14.2, J15.2, J16.2, J17.2, J18.2, J19.2, J20.2, J21.2, J22.2, J23.2, J24.2, J25.2, J26.2, J27.2, J28.2, J29.2, J30.2, J31.2, J32.2, J33.2, J34.2, J35.2, J36.2, J37.2, J38.2, J39.2, J40.2, J41.2, J42.2, J43.2, J44.2, J45.2, J46.2, J47.2, J48.2, J49.2, J50.2, J51.2, J52.2, J53.2, J54.2, J55.2, J56.2, J57.2, J58.2, J59.2, J60.2, J61.2, J62.2, J63.2, J64.2, J65.2, J66.2, J67.2, J68.2, J69.2, J70.2, J71.2, J72.2, J73.2, J74.2, J75.2, J76.2, J77.2, J78.2, J79.2, J80.2, J81.2, J82.2, J83.2, J84.2, J85.2, J86.2, J87.2, J88.2, J89.2, J90.2, J91.2, J92.2, J93.2, J94.2, J95.2, J96.2, J97.2, J97#2.2, J98.2, J98#2.2, J99.2, J99#2.2, J100.2, J100#2.2, J101.2, J101#2.2, J102.2, J102#2.2, J103.2, J103#2.2, J104.2, J104#2.2, J105.2, J105#2.2, J106.2, J106#2.2, J107.2, J107#2.2, J108.2, J108#2.2, J109.2, J109#2.2, J110.2, J110#2.2, J111.2, J111#2.2, M2.2 (-), M2#2.2 (-), M2#3.2 (-), M2#4.2 (-), M3.2 (-), M4.2 (-), M5.2 (-), M6.2 (-), M7.2 (-), M8.2 (-), M9.2 (-), M10.2 (-), M11.2 (-), M12.2 (-), M13.2 (-), M14.2 (-), M15.2 (-), M16.2 (-), M17.2 (-), M18.2 (-)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

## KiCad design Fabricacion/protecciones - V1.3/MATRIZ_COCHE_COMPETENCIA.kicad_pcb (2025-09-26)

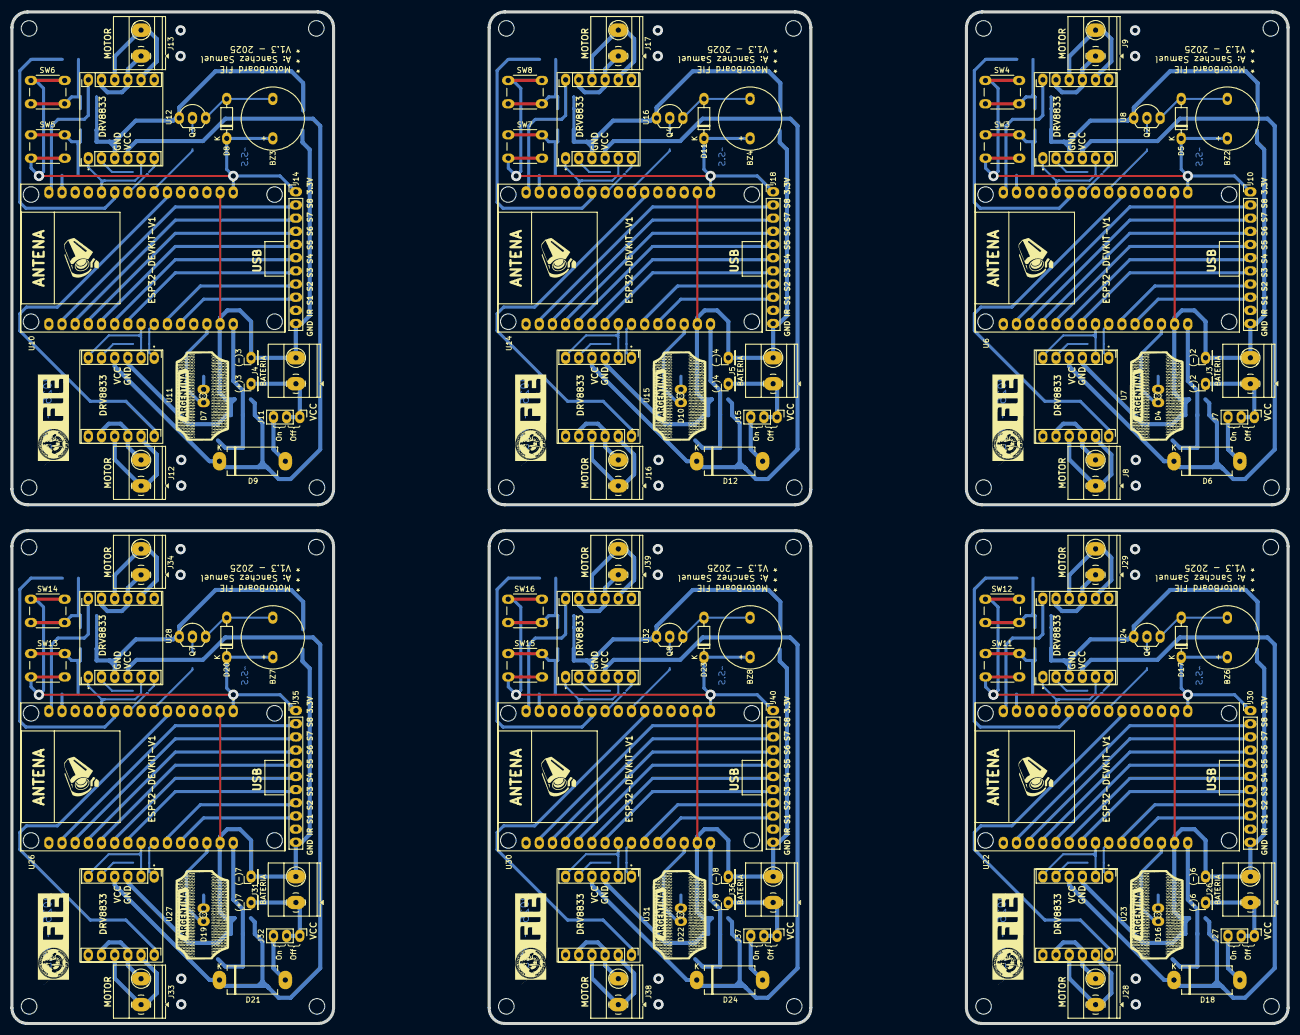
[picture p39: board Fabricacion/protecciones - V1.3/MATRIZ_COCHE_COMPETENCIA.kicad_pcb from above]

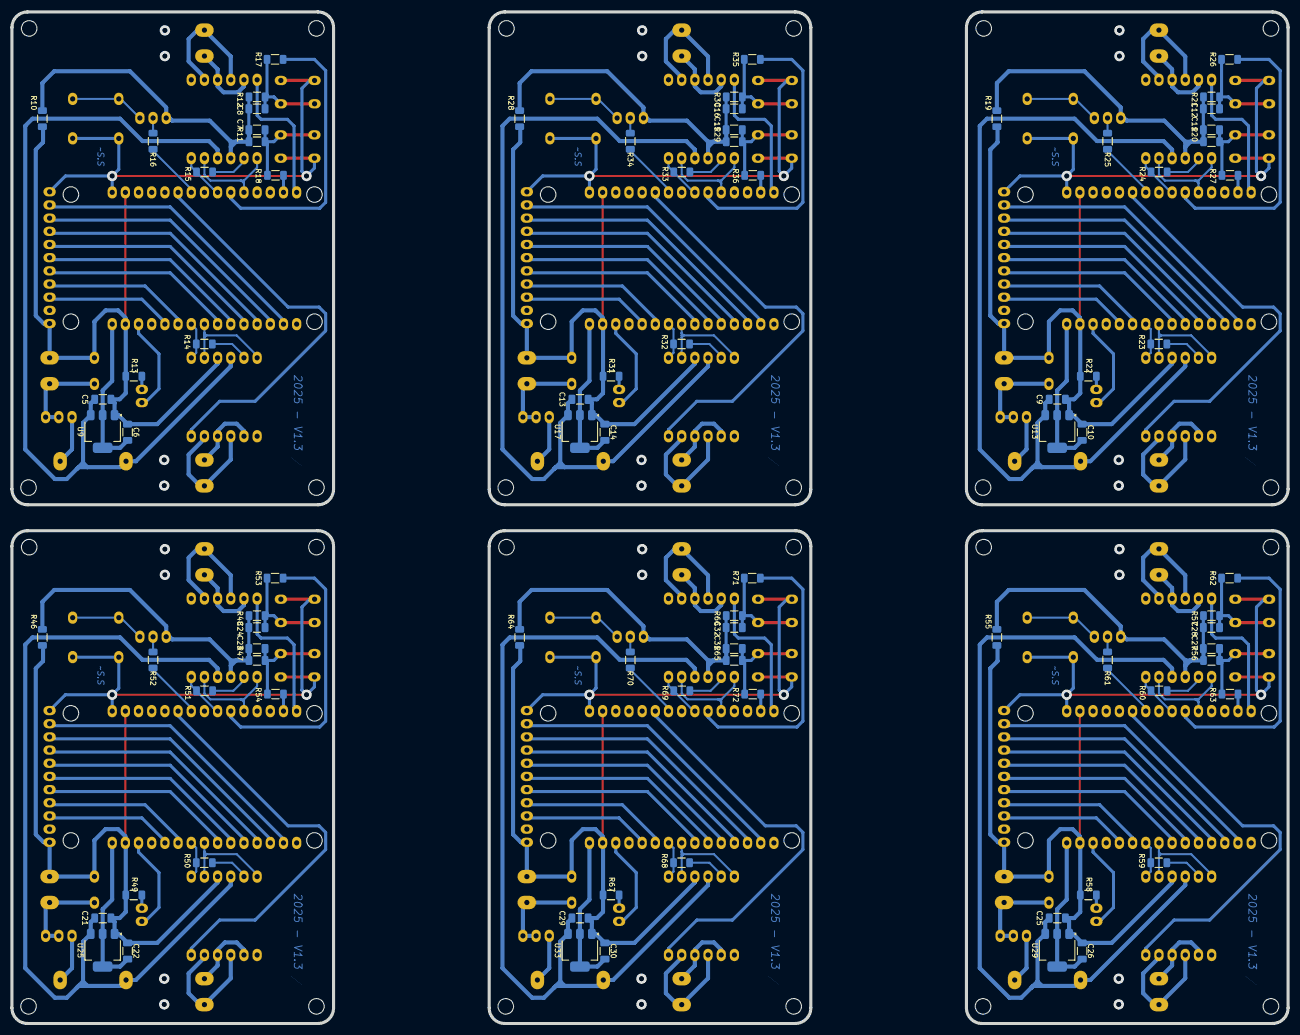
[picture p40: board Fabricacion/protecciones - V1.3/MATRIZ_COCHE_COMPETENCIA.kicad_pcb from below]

Board: 2 copper layers, 246.0 x 195.0 mm, 210 parts (84 on the bottom side), 35 nets.

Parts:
(+)2, (+)3, (+)4, (+)6, (+)7, (+)8: TestPoint; PinHeader_1x01_P2.54mm_Vertical
(-)2, (-)3, (-)4, (-)6, (-)7, (-)8: TestPoint; PinHeader_1x01_P2.54mm_Vertical
BZ2, BZ3, BZ4, BZ6, BZ7, BZ8: Buzzer; MagneticBuzzer_ProSignal_ABI-009-RC
C5, C7, C8, C9, C11, C12, C13, C15, C16, C21, C23, C24, C25, C27, C28, C29, C31, C32: 100n; C_1206_3216Metric_Pad1.33x1.80mm_HandSolder
C6, C10, C14, C22, C26, C30: 1u; C_1206_3216Metric_Pad1.33x1.80mm_HandSolder
D4, D7, D10, D16, D19, D22: LED_RED; LED_D5.0mm
D5, D8, D11, D17, D20, D23: 1N4148; D_DO-35_SOD27_P7.62mm_Horizontal
D6, D9, D12, D18, D21, D24: 1N5822; D_DO-201AD_P12.70mm_Horizontal
H5, H6, H7, H8, H9, H10, H11, H12, H13, H14, H15, H16, H21, H22, H23, H24, H25, H26, H27, H28, H29, H30, H31, H32: MountingHole; MountingHole_3mm
J3, J4, J5, J26, J31, J36: BAT; TerminalBlock_Phoenix_MKDS-1,5-2_1x02_P5.00mm_Horizontal
J7, J11, J15, J27, J32, J37: SWITCH; PinHeader_1x03_P2.54mm_Vertical
J8, J12, J16, J28, J33, J38: M1; TerminalBlock_Phoenix_MKDS-1,5-2_1x02_P5.00mm_Horizontal
J9, J13, J17, J29, J34, J39: M2; TerminalBlock_Phoenix_MKDS-1,5-2_1x02_P5.00mm_Horizontal
J10, J14, J18, J30, J35, J40: SENSORES; PinHeader_1x11_P2.54mm_Vertical
Q2, Q3, Q4, Q6, Q7, Q8: 2N3904; TO-92_Inline_Wide
R10, R14, R15, R19, R23, R24, R28, R32, R33, R46, R50, R51, R55, R59, R60, R64, R68, R69: 0; R_1206_3216Metric_Pad1.30x1.75mm_HandSolder
R11, R12, R20, R21, R29, R30, R47, R48, R56, R57, R65, R66: 10k; R_1206_3216Metric_Pad1.30x1.75mm_HandSolder
R13, R22, R31, R49, R58, R67: 220; R_1206_3216Metric_Pad1.30x1.75mm_HandSolder
R16, R25, R34, R52, R61, R70: 1k; R_1206_3216Metric_Pad1.30x1.75mm_HandSolder
R17, R18, R26, R27, R35, R36, R53, R54, R62, R63, R71, R72: 100; R_1206_3216Metric_Pad1.30x1.75mm_HandSolder
SW3, SW4, SW5, SW6, SW7, SW8, SW11, SW12, SW13, SW14, SW15, SW16: SW_Push; SW_PUSH_6mm_H5mm
U6, U10, U14, U22, U26, U30: ESP32-DEVKIT-V1; MODULE_ESP32_DEVKIT_V1
U7, U8, U11, U12, U15, U16, U23, U24, U27, U28, U31, U32: DRV8833
U9, U13, U17, U25, U29, U33: AMS1117; SOT-223-3_TabPin2

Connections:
+3.3V: BZ2.1 (+), BZ3.1 (+), BZ4.1 (+), BZ6.1 (+), BZ7.1 (+), BZ8.1 (+), D5.1 (K), D8.1 (K), D11.1 (K), D17.1 (K), D20.1 (K), D23.1 (K), J10.1, J14.1, J18.1, J30.1, J35.1, J40.1, SW3.1, SW4.1, SW5.1, SW6.1, SW7.1, SW8.1, SW11.1, SW12.1, SW13.1, SW14.1, SW15.1, SW16.1, U6.1 (3V3), U10.1 (3V3), U14.1 (3V3), U22.1 (3V3), U26.1 (3V3), U30.1 (3V3)
+5V: C6.1, C10.1, C14.1, C22.1, C26.1, C30.1, U6.30 (VIN), U9.2 (VO), U10.30 (VIN), U13.2 (VO), U14.30 (VIN), U17.2 (VO), U22.30 (VIN), U25.2 (VO), U26.30 (VIN), U29.2 (VO), U30.30 (VIN), U33.2 (VO)
/BUZZER: R16.1, R25.1, R34.1, R52.1, R61.1, R70.1, U6.7 (TX2), U10.7 (TX2), U14.7 (TX2), U22.7 (TX2), U26.7 (TX2), U30.7 (TX2)
/IN_M1_A: R14.1, R23.1, R32.1, R50.1, R59.1, R68.1, U6.24 (D26), U7.1 (IN4), U10.24 (D26), U11.1 (IN4), U14.24 (D26), U15.1 (IN4), U22.24 (D26), U23.1 (IN4), U26.24 (D26), U27.1 (IN4), U30.24 (D26), U31.1 (IN4)
/IN_M1_B: U6.23 (D25), U7.2 (IN3), U7.6 (IN1), U10.23 (D25), U11.2 (IN3), U11.6 (IN1), U14.23 (D25), U15.2 (IN3), U15.6 (IN1), U22.23 (D25), U23.2 (IN3), U23.6 (IN1), U26.23 (D25), U27.2 (IN3), U27.6 (IN1), U30.23 (D25), U31.2 (IN3), U31.6 (IN1)
/IN_M2_A: U6.11 (D21), U8.1 (IN4), U8.5 (IN2), U10.11 (D21), U12.1 (IN4), U12.5 (IN2), U14.11 (D21), U16.1 (IN4), U16.5 (IN2), U22.11 (D21), U24.1 (IN4), U24.5 (IN2), U26.11 (D21), U28.1 (IN4), U28.5 (IN2), U30.11 (D21), U32.1 (IN4), U32.5 (IN2)
/IN_M2_B: R15.1, R24.1, R33.1, R51.1, R60.1, R69.1, U6.9 (D18), U8.6 (IN1), U10.9 (D18), U12.6 (IN1), U14.9 (D18), U16.6 (IN1), U22.9 (D18), U24.6 (IN1), U26.9 (D18), U28.6 (IN1), U30.9 (D18), U32.6 (IN1)
/LED_LARGADA: D4.2 (A), D7.2 (A), D10.2 (A), D16.2 (A), D19.2 (A), D22.2 (A), U6.28 (D13), U10.28 (D13), U14.28 (D13), U22.28 (D13), U26.28 (D13), U30.28 (D13)
/S1: J10.9, J14.9, J18.9, J30.9, J35.9, J40.9, U6.26 (D14), U10.26 (D14), U14.26 (D14), U22.26 (D14), U26.26 (D14), U30.26 (D14)
/S2: J10.8, J14.8, J18.8, J30.8, J35.8, J40.8, U6.25 (D27), U10.25 (D27), U14.25 (D27), U22.25 (D27), U26.25 (D27), U30.25 (D27)
/S3: J10.7, J14.7, J18.7, J30.7, J35.7, J40.7, U6.22 (D33), U10.22 (D33), U14.22 (D33), U22.22 (D33), U26.22 (D33), U30.22 (D33)
/S4: J10.6, J14.6, J18.6, J30.6, J35.6, J40.6, U6.21 (D32), U10.21 (D32), U14.21 (D32), U22.21 (D32), U26.21 (D32), U30.21 (D32)
/S5: J10.5, J14.5, J18.5, J30.5, J35.5, J40.5, U6.20 (D35), U10.20 (D35), U14.20 (D35), U22.20 (D35), U26.20 (D35), U30.20 (D35)
/S6: J10.4, J14.4, J18.4, J30.4, J35.4, J40.4, U6.19 (D34), U10.19 (D34), U14.19 (D34), U22.19 (D34), U26.19 (D34), U30.19 (D34)
/S7: J10.3, J14.3, J18.3, J30.3, J35.3, J40.3, U6.18 (VN), U10.18 (VN), U14.18 (VN), U22.18 (VN), U26.18 (VN), U30.18 (VN)
/S8: J10.2, J14.2, J18.2, J30.2, J35.2, J40.2, U6.17 (VP), U10.17 (VP), U14.17 (VP), U22.17 (VP), U26.17 (VP), U30.17 (VP)
/SLEEP_M1: U6.6 (RX2), U7.12 (SLEEP), U10.6 (RX2), U11.12 (SLEEP), U14.6 (RX2), U15.12 (SLEEP), U22.6 (RX2), U23.12 (SLEEP), U26.6 (RX2), U27.12 (SLEEP), U30.6 (RX2), U31.12 (SLEEP)
/SLEEP_M2: U6.15 (D23), U8.12 (SLEEP), U10.15 (D23), U12.12 (SLEEP), U14.15 (D23), U16.12 (SLEEP), U22.15 (D23), U24.12 (SLEEP), U26.15 (D23), U28.12 (SLEEP), U30.15 (D23), U32.12 (SLEEP)
/SW1: R18.2, R27.2, R36.2, R54.2, R63.2, R72.2, U6.14 (D22), U10.14 (D22), U14.14 (D22), U22.14 (D22), U26.14 (D22), U30.14 (D22)
/SW2: R17.2, R26.2, R35.2, R53.2, R62.2, R71.2, U6.10 (D19), U10.10 (D19), U14.10 (D19), U22.10 (D19), U26.10 (D19), U30.10 (D19)
GND: (-)2.1, (-)3.1, (-)4.1, (-)6.1, (-)7.1, (-)8.1, C5.2, C6.2, C7.2, C8.2, C9.2, C10.2, C11.2, C12.2, C13.2, C14.2, C15.2, C16.2, C21.2, C22.2, C23.2, C24.2, C25.2, C26.2, C27.2, C28.2, C29.2, C30.2, C31.2, C32.2, J3.2, J4.2, J5.2, J10.11, J14.11, J18.11, J26.2, J30.11, J31.2, J35.11, J36.2, J40.11, Q2.1 (E), Q3.1 (E), Q4.1 (E), Q6.1 (E), Q7.1 (E), Q8.1 (E), R10.1, R10.2, R11.2, R12.2, R13.2, R19.1, R19.2, R20.2, R21.2, R22.2, R28.1, R28.2, R29.2, R30.2, R31.2, R46.1, R46.2, R47.2, R48.2, R49.2, R55.1, R55.2, R56.2, R57.2, R58.2, R64.1, R64.2, R65.2, R66.2, R67.2, U6.2 (GND), U6.29 (GND), U7.3 (GND), U8.3 (GND), U9.1 (ADJ), U10.2 (GND), U10.29 (GND), U11.3 (GND), U12.3 (GND), U13.1 (ADJ), U14.2 (GND), U14.29 (GND), U15.3 (GND), U16.3 (GND), U17.1 (ADJ), U22.2 (GND), U22.29 (GND), U23.3 (GND), U24.3 (GND), U25.1 (ADJ), U26.2 (GND), U26.29 (GND), U27.3 (GND), U28.3 (GND), U29.1 (ADJ), U30.2 (GND), U30.29 (GND), U31.3 (GND), U32.3 (GND), U33.1 (ADJ)
unnamed: BZ2.2 (-), BZ3.2 (-), BZ4.2 (-), BZ6.2 (-), BZ7.2 (-), BZ8.2 (-), D5.2 (A), D8.2 (A), D11.2 (A), D17.2 (A), D20.2 (A), D23.2 (A), Q2.3 (C), Q3.3 (C), Q4.3 (C), Q6.3 (C), Q7.3 (C), Q8.3 (C)
unnamed: C7.1, C11.1, C15.1, C23.1, C27.1, C31.1, R11.1, R18.1, R20.1, R27.1, R29.1, R36.1, R47.1, R54.1, R56.1, R63.1, R65.1, R72.1, SW3.2, SW5.2, SW7.2, SW11.2, SW13.2, SW15.2
unnamed: C8.1, C12.1, C16.1, C24.1, C28.1, C32.1, R12.1, R17.1, R21.1, R26.1, R30.1, R35.1, R48.1, R53.1, R57.1, R62.1, R66.1, R71.1, SW4.2, SW6.2, SW8.2, SW12.2, SW14.2, SW16.2
unnamed: D4.1 (K), D7.1 (K), D10.1 (K), D16.1 (K), D19.1 (K), D22.1 (K), R13.1, R22.1, R31.1, R49.1, R58.1, R67.1
unnamed: D6.2 (A), D9.2 (A), D12.2 (A), D18.2 (A), D21.2 (A), D24.2 (A), J7.3, J11.3, J15.3, J27.3, J32.3, J37.3
unnamed: (+)2.1, (+)3.1, (+)4.1, (+)6.1, (+)7.1, (+)8.1, J3.1, J4.1, J5.1, J7.1, J7.2, J11.1, J11.2, J15.1, J15.2, J26.1, J27.1, J27.2, J31.1, J32.1, J32.2, J36.1, J37.1, J37.2
unnamed: J8.1, J12.1, J16.1, J28.1, J33.1, J38.1, U7.9 (OUT3), U7.11 (OUT1), U11.9 (OUT3), U11.11 (OUT1), U15.9 (OUT3), U15.11 (OUT1), U23.9 (OUT3), U23.11 (OUT1), U27.9 (OUT3), U27.11 (OUT1), U31.9 (OUT3), U31.11 (OUT1)
unnamed: J8.2, J12.2, J16.2, J28.2, J33.2, J38.2, U7.8 (OUT4), U7.10 (OUT2), U11.8 (OUT4), U11.10 (OUT2), U15.8 (OUT4), U15.10 (OUT2), U23.8 (OUT4), U23.10 (OUT2), U27.8 (OUT4), U27.10 (OUT2), U31.8 (OUT4), U31.10 (OUT2)
unnamed: J9.1, J13.1, J17.1, J29.1, J34.1, J39.1, U8.9 (OUT3), U8.11 (OUT1), U12.9 (OUT3), U12.11 (OUT1), U16.9 (OUT3), U16.11 (OUT1), U24.9 (OUT3), U24.11 (OUT1), U28.9 (OUT3), U28.11 (OUT1), U32.9 (OUT3), U32.11 (OUT1)
unnamed: J9.2, J13.2, J17.2, J29.2, J34.2, J39.2, U8.8 (OUT4), U8.10 (OUT2), U12.8 (OUT4), U12.10 (OUT2), U16.8 (OUT4), U16.10 (OUT2), U24.8 (OUT4), U24.10 (OUT2), U28.8 (OUT4), U28.10 (OUT2), U32.8 (OUT4), U32.10 (OUT2)
unnamed: Q2.2 (B), Q3.2 (B), Q4.2 (B), Q6.2 (B), Q7.2 (B), Q8.2 (B), R16.2, R25.2, R34.2, R52.2, R61.2, R70.2
unnamed: R14.2, R23.2, R32.2, R50.2, R59.2, R68.2, U7.5 (IN2), U11.5 (IN2), U15.5 (IN2), U23.5 (IN2), U27.5 (IN2), U31.5 (IN2)
unnamed: R15.2, R24.2, R33.2, R51.2, R60.2, R69.2, U8.2 (IN3), U12.2 (IN3), U16.2 (IN3), U24.2 (IN3), U28.2 (IN3), U32.2 (IN3)
VCC: C5.1, C9.1, C13.1, C21.1, C25.1, C29.1, D6.1 (K), D9.1 (K), D12.1 (K), D18.1 (K), D21.1 (K), D24.1 (K), U7.4 (VCC), U8.4 (VCC), U9.3 (VI), U11.4 (VCC), U12.4 (VCC), U13.3 (VI), U15.4 (VCC), U16.4 (VCC), U17.3 (VI), U23.4 (VCC), U24.4 (VCC), U25.3 (VI), U27.4 (VCC), U28.4 (VCC), U29.3 (VI), U31.4 (VCC), U32.4 (VCC), U33.3 (VI)

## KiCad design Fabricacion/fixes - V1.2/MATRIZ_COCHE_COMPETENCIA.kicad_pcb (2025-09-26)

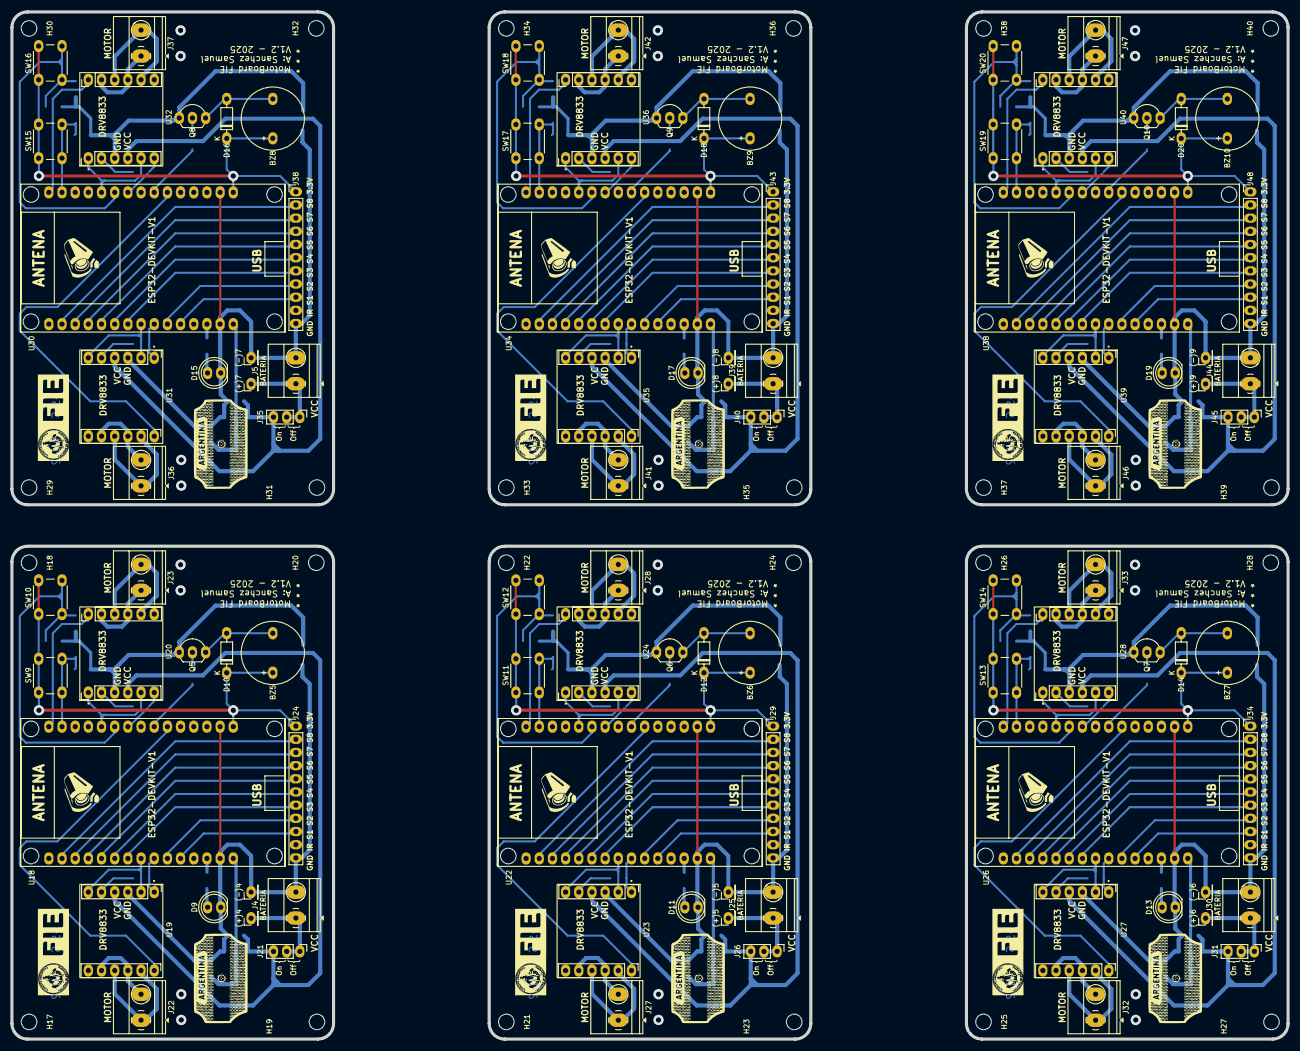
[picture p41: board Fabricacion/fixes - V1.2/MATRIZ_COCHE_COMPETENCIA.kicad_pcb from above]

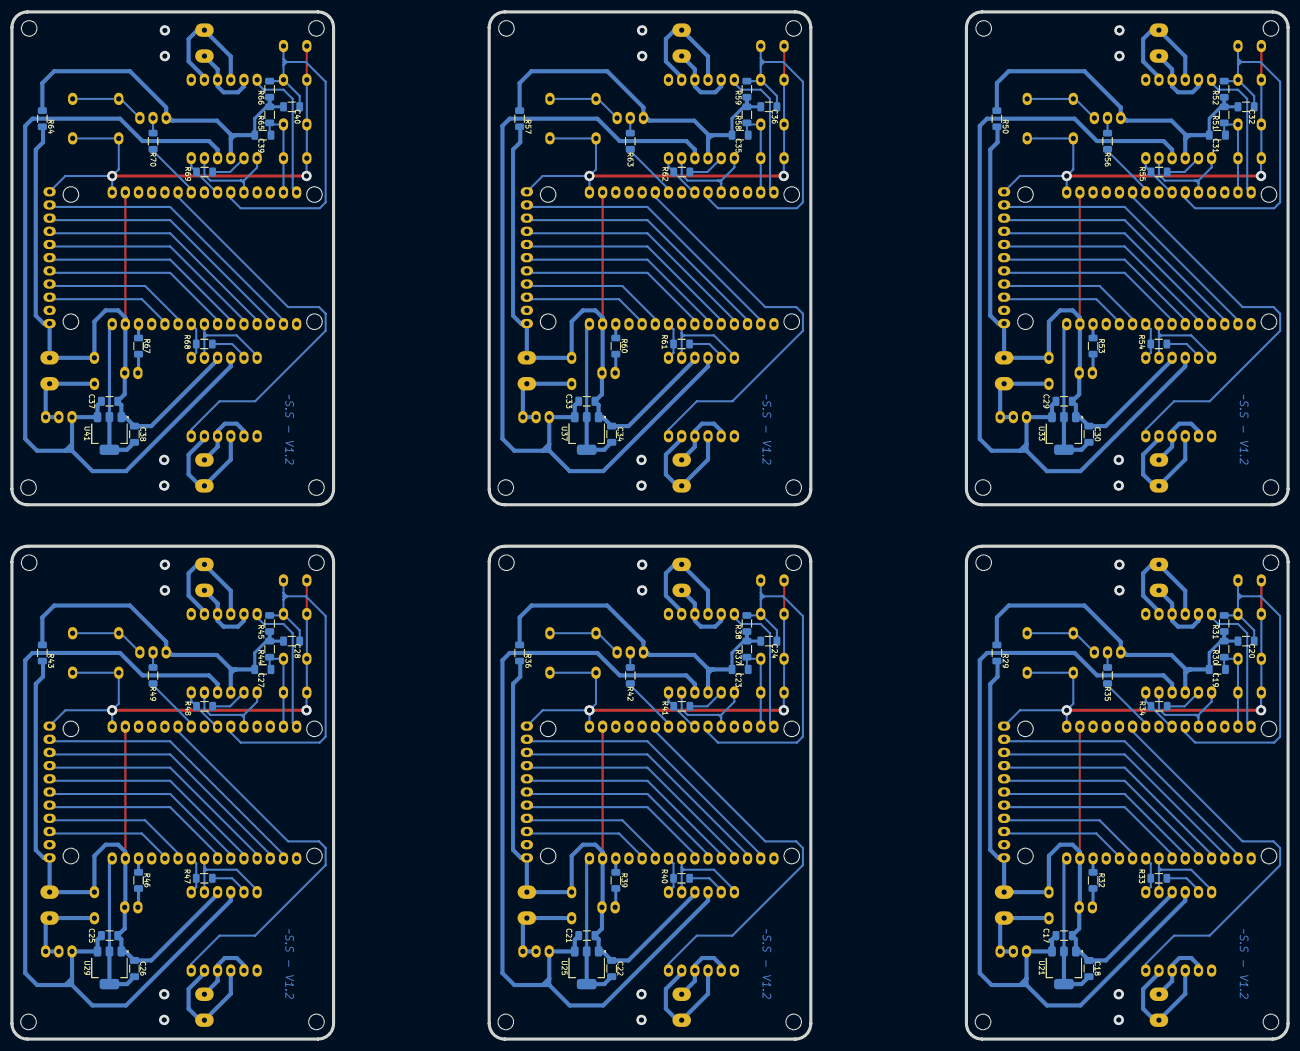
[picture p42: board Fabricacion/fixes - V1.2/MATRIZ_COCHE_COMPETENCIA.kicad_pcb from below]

Board: 2 copper layers, 246.0 x 198.0 mm, 192 parts (72 on the bottom side), 32 nets.

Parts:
(+)4, (+)5, (+)6, (+)7, (+)8, (+)9: TestPoint; PinHeader_1x01_P2.54mm_Vertical
(-)4, (-)5, (-)6, (-)7, (-)8, (-)9: TestPoint; PinHeader_1x01_P2.54mm_Vertical
BZ5, BZ6, BZ7, BZ8, BZ9, BZ10: Buzzer; MagneticBuzzer_ProSignal_ABI-009-RC
C17, C21, C25, C29, C33, C37: 0.33u; C_1206_3216Metric_Pad1.33x1.80mm_HandSolder
C18, C19, C20, C22, C23, C24, C26, C27, C28, C30, C31, C32, C34, C35, C36, C38, C39, C40: 0.1u; C_1206_3216Metric_Pad1.33x1.80mm_HandSolder
D9, D11, D13, D15, D17, D19: LED_RED; LED_D5.0mm
D10, D12, D14, D16, D18, D20: 1N4148; D_DO-35_SOD27_P7.62mm_Horizontal
H17, H18, H19, H20, H21, H22, H23, H24, H25, H26, H27, H28, H29, H30, H31, H32, H33, H34, H35, H36, H37, H38, H39, H40: MountingHole; MountingHole_3mm
J4, J5, J25, J30, J39, J44: BAT; TerminalBlock_Phoenix_MKDS-1,5-2_1x02_P5.00mm_Horizontal
J21, J26, J31, J35, J40, J45: SWITCH; PinHeader_1x03_P2.54mm_Vertical
J22, J27, J32, J36, J41, J46: M1; TerminalBlock_Phoenix_MKDS-1,5-2_1x02_P5.00mm_Horizontal
J23, J28, J33, J37, J42, J47: M2; TerminalBlock_Phoenix_MKDS-1,5-2_1x02_P5.00mm_Horizontal
J24, J29, J34, J38, J43, J48: SENSORES; PinHeader_1x11_P2.54mm_Vertical
Q5, Q6, Q7, Q8, Q9, Q10: 2N3904; TO-92_Inline_Wide
R29, R33, R34, R36, R40, R41, R43, R47, R48, R50, R54, R55, R57, R61, R62, R64, R68, R69: 0; R_1206_3216Metric_Pad1.30x1.75mm_HandSolder
R30, R31, R37, R38, R44, R45, R51, R52, R58, R59, R65, R66: 10k; R_1206_3216Metric_Pad1.30x1.75mm_HandSolder
R32, R39, R46, R53, R60, R67: 220; R_1206_3216Metric_Pad1.30x1.75mm_HandSolder
R35, R42, R49, R56, R63, R70: 1k; R_1206_3216Metric_Pad1.30x1.75mm_HandSolder
SW9, SW10, SW11, SW12, SW13, SW14, SW15, SW16, SW17, SW18, SW19, SW20: SW_Push; SW_PUSH_6mm_H5mm
U18, U22, U26, U30, U34, U38: ESP32-DEVKIT-V1; MODULE_ESP32_DEVKIT_V1
U19, U20, U23, U24, U27, U28, U31, U32, U35, U36, U39, U40: DRV8833
U21, U25, U29, U33, U37, U41: AMS1117; SOT-223-3_TabPin2

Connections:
+3.3V: BZ5.1 (+), BZ6.1 (+), BZ7.1 (+), BZ8.1 (+), BZ9.1 (+), BZ10.1 (+), D10.1 (K), D12.1 (K), D14.1 (K), D16.1 (K), D18.1 (K), D20.1 (K), J24.1, J29.1, J34.1, J38.1, J43.1, J48.1, SW9.1, SW10.1, SW11.1, SW12.1, SW13.1, SW14.1, SW15.1, SW16.1, SW17.1, SW18.1, SW19.1, SW20.1, U18.1 (3V3), U22.1 (3V3), U26.1 (3V3), U30.1 (3V3), U34.1 (3V3), U38.1 (3V3)
+5V: C18.1, C22.1, C26.1, C30.1, C34.1, C38.1, U18.30 (VIN), U21.2 (VO), U22.30 (VIN), U25.2 (VO), U26.30 (VIN), U29.2 (VO), U30.30 (VIN), U33.2 (VO), U34.30 (VIN), U37.2 (VO), U38.30 (VIN), U41.2 (VO)
/BUZZER: R35.1, R42.1, R49.1, R56.1, R63.1, R70.1, U18.7 (TX2), U22.7 (TX2), U26.7 (TX2), U30.7 (TX2), U34.7 (TX2), U38.7 (TX2)
/IN_M1_A: R33.1, R40.1, R47.1, R54.1, R61.1, R68.1, U18.24 (D26), U19.1 (IN4), U22.24 (D26), U23.1 (IN4), U26.24 (D26), U27.1 (IN4), U30.24 (D26), U31.1 (IN4), U34.24 (D26), U35.1 (IN4), U38.24 (D26), U39.1 (IN4)
/IN_M1_B: U18.23 (D25), U19.2 (IN3), U19.6 (IN1), U22.23 (D25), U23.2 (IN3), U23.6 (IN1), U26.23 (D25), U27.2 (IN3), U27.6 (IN1), U30.23 (D25), U31.2 (IN3), U31.6 (IN1), U34.23 (D25), U35.2 (IN3), U35.6 (IN1), U38.23 (D25), U39.2 (IN3), U39.6 (IN1)
/IN_M2_A: U18.11 (D21), U20.1 (IN4), U20.5 (IN2), U22.11 (D21), U24.1 (IN4), U24.5 (IN2), U26.11 (D21), U28.1 (IN4), U28.5 (IN2), U30.11 (D21), U32.1 (IN4), U32.5 (IN2), U34.11 (D21), U36.1 (IN4), U36.5 (IN2), U38.11 (D21), U40.1 (IN4), U40.5 (IN2)
/IN_M2_B: R34.1, R41.1, R48.1, R55.1, R62.1, R69.1, U18.9 (D18), U20.6 (IN1), U22.9 (D18), U24.6 (IN1), U26.9 (D18), U28.6 (IN1), U30.9 (D18), U32.6 (IN1), U34.9 (D18), U36.6 (IN1), U38.9 (D18), U40.6 (IN1)
/LED_LARGADA: R32.1, R39.1, R46.1, R53.1, R60.1, R67.1, U18.28 (D13), U22.28 (D13), U26.28 (D13), U30.28 (D13), U34.28 (D13), U38.28 (D13)
/S1: J24.9, J29.9, J34.9, J38.9, J43.9, J48.9, U18.26 (D14), U22.26 (D14), U26.26 (D14), U30.26 (D14), U34.26 (D14), U38.26 (D14)
/S2: J24.8, J29.8, J34.8, J38.8, J43.8, J48.8, U18.25 (D27), U22.25 (D27), U26.25 (D27), U30.25 (D27), U34.25 (D27), U38.25 (D27)
/S3: J24.7, J29.7, J34.7, J38.7, J43.7, J48.7, U18.22 (D33), U22.22 (D33), U26.22 (D33), U30.22 (D33), U34.22 (D33), U38.22 (D33)
/S4: J24.6, J29.6, J34.6, J38.6, J43.6, J48.6, U18.21 (D32), U22.21 (D32), U26.21 (D32), U30.21 (D32), U34.21 (D32), U38.21 (D32)
/S5: J24.5, J29.5, J34.5, J38.5, J43.5, J48.5, U18.20 (D35), U22.20 (D35), U26.20 (D35), U30.20 (D35), U34.20 (D35), U38.20 (D35)
/S6: J24.4, J29.4, J34.4, J38.4, J43.4, J48.4, U18.19 (D34), U22.19 (D34), U26.19 (D34), U30.19 (D34), U34.19 (D34), U38.19 (D34)
/S7: J24.3, J29.3, J34.3, J38.3, J43.3, J48.3, U18.18 (VN), U22.18 (VN), U26.18 (VN), U30.18 (VN), U34.18 (VN), U38.18 (VN)
/S8: J24.2, J29.2, J34.2, J38.2, J43.2, J48.2, U18.17 (VP), U22.17 (VP), U26.17 (VP), U30.17 (VP), U34.17 (VP), U38.17 (VP)
/SLEEP_M1: U18.6 (RX2), U19.12 (SLEEP), U22.6 (RX2), U23.12 (SLEEP), U26.6 (RX2), U27.12 (SLEEP), U30.6 (RX2), U31.12 (SLEEP), U34.6 (RX2), U35.12 (SLEEP), U38.6 (RX2), U39.12 (SLEEP)
/SLEEP_M2: U18.15 (D23), U20.12 (SLEEP), U22.15 (D23), U24.12 (SLEEP), U26.15 (D23), U28.12 (SLEEP), U30.15 (D23), U32.12 (SLEEP), U34.15 (D23), U36.12 (SLEEP), U38.15 (D23), U40.12 (SLEEP)
/SW1: C19.1, C23.1, C27.1, C31.1, C35.1, C39.1, R30.1, R37.1, R44.1, R51.1, R58.1, R65.1, SW9.2, SW11.2, SW13.2, SW15.2, SW17.2, SW19.2, U18.14 (D22), U22.14 (D22), U26.14 (D22), U30.14 (D22), U34.14 (D22), U38.14 (D22)
/SW2: C20.1, C24.1, C28.1, C32.1, C36.1, C40.1, R31.1, R38.1, R45.1, R52.1, R59.1, R66.1, SW10.2, SW12.2, SW14.2, SW16.2, SW18.2, SW20.2, U18.10 (D19), U22.10 (D19), U26.10 (D19), U30.10 (D19), U34.10 (D19), U38.10 (D19)
GND: (-)4.1, (-)5.1, (-)6.1, (-)7.1, (-)8.1, (-)9.1, C17.2, C18.2, C19.2, C20.2, C21.2, C22.2, C23.2, C24.2, C25.2, C26.2, C27.2, C28.2, C29.2, C30.2, C31.2, C32.2, C33.2, C34.2, C35.2, C36.2, C37.2, C38.2, C39.2, C40.2, D9.1 (K), D11.1 (K), D13.1 (K), D15.1 (K), D17.1 (K), D19.1 (K), J4.2, J5.2, J24.11, J25.2, J29.11, J30.2, J34.11, J38.11, J39.2, J43.11, J44.2, J48.11, Q5.1 (E), Q6.1 (E), Q7.1 (E), Q8.1 (E), Q9.1 (E), Q10.1 (E), R29.1, R29.2, R30.2, R31.2, R36.1, R36.2, R37.2, R38.2, R43.1, R43.2, R44.2, R45.2, R50.1, R50.2, R51.2, R52.2, R57.1, R57.2, R58.2, R59.2, R64.1, R64.2, R65.2, R66.2, U18.2 (GND), U18.29 (GND), U19.3 (GND), U20.3 (GND), U21.1 (ADJ), U22.2 (GND), U22.29 (GND), U23.3 (GND), U24.3 (GND), U25.1 (ADJ), U26.2 (GND), U26.29 (GND), U27.3 (GND), U28.3 (GND), U29.1 (ADJ), U30.2 (GND), U30.29 (GND), U31.3 (GND), U32.3 (GND), U33.1 (ADJ), U34.2 (GND), U34.29 (GND), U35.3 (GND), U36.3 (GND), U37.1 (ADJ), U38.2 (GND), U38.29 (GND), U39.3 (GND), U40.3 (GND), U41.1 (ADJ)
unnamed: BZ5.2 (-), BZ6.2 (-), BZ7.2 (-), BZ8.2 (-), BZ9.2 (-), BZ10.2 (-), D10.2 (A), D12.2 (A), D14.2 (A), D16.2 (A), D18.2 (A), D20.2 (A), Q5.3 (C), Q6.3 (C), Q7.3 (C), Q8.3 (C), Q9.3 (C), Q10.3 (C)
unnamed: D9.2 (A), D11.2 (A), D13.2 (A), D15.2 (A), D17.2 (A), D19.2 (A), R32.2, R39.2, R46.2, R53.2, R60.2, R67.2
unnamed: (+)4.1, (+)5.1, (+)6.1, (+)7.1, (+)8.1, (+)9.1, J4.1, J5.1, J21.1, J21.2, J25.1, J26.1, J26.2, J30.1, J31.1, J31.2, J35.1, J35.2, J39.1, J40.1, J40.2, J44.1, J45.1, J45.2
unnamed: J22.1, J27.1, J32.1, J36.1, J41.1, J46.1, U19.9 (OUT3), U19.11 (OUT1), U23.9 (OUT3), U23.11 (OUT1), U27.9 (OUT3), U27.11 (OUT1), U31.9 (OUT3), U31.11 (OUT1), U35.9 (OUT3), U35.11 (OUT1), U39.9 (OUT3), U39.11 (OUT1)
unnamed: J22.2, J27.2, J32.2, J36.2, J41.2, J46.2, U19.8 (OUT4), U19.10 (OUT2), U23.8 (OUT4), U23.10 (OUT2), U27.8 (OUT4), U27.10 (OUT2), U31.8 (OUT4), U31.10 (OUT2), U35.8 (OUT4), U35.10 (OUT2), U39.8 (OUT4), U39.10 (OUT2)
unnamed: J23.1, J28.1, J33.1, J37.1, J42.1, J47.1, U20.9 (OUT3), U20.11 (OUT1), U24.9 (OUT3), U24.11 (OUT1), U28.9 (OUT3), U28.11 (OUT1), U32.9 (OUT3), U32.11 (OUT1), U36.9 (OUT3), U36.11 (OUT1), U40.9 (OUT3), U40.11 (OUT1)
unnamed: J23.2, J28.2, J33.2, J37.2, J42.2, J47.2, U20.8 (OUT4), U20.10 (OUT2), U24.8 (OUT4), U24.10 (OUT2), U28.8 (OUT4), U28.10 (OUT2), U32.8 (OUT4), U32.10 (OUT2), U36.8 (OUT4), U36.10 (OUT2), U40.8 (OUT4), U40.10 (OUT2)
unnamed: Q5.2 (B), Q6.2 (B), Q7.2 (B), Q8.2 (B), Q9.2 (B), Q10.2 (B), R35.2, R42.2, R49.2, R56.2, R63.2, R70.2
unnamed: R33.2, R40.2, R47.2, R54.2, R61.2, R68.2, U19.5 (IN2), U23.5 (IN2), U27.5 (IN2), U31.5 (IN2), U35.5 (IN2), U39.5 (IN2)
unnamed: R34.2, R41.2, R48.2, R55.2, R62.2, R69.2, U20.2 (IN3), U24.2 (IN3), U28.2 (IN3), U32.2 (IN3), U36.2 (IN3), U40.2 (IN3)
VCC: C17.1, C21.1, C25.1, C29.1, C33.1, C37.1, J21.3, J26.3, J31.3, J35.3, J40.3, J45.3, U19.4 (VCC), U20.4 (VCC), U21.3 (VI), U23.4 (VCC), U24.4 (VCC), U25.3 (VI), U27.4 (VCC), U28.4 (VCC), U29.3 (VI), U31.4 (VCC), U32.4 (VCC), U33.3 (VI), U35.4 (VCC), U36.4 (VCC), U37.3 (VI), U39.4 (VCC), U40.4 (VCC), U41.3 (VI)

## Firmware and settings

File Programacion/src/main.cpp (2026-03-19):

/**
 @file main.cpp
 @brief Archivo principal del Seguidor de Línea Competencia Robótica.
 @details Contiene el flujo principal del programa, la inicialización del hardware, 
 el lazo de control (loop) y las definiciones de las funciones de estado de la FSM.
 @author Legion de Ohm
 */

#include <Arduino.h>
//#include <IRremote.hpp>
#include "buzzer.hpp"
#include "interrupciones.hpp"
#include "config.hpp"
#include "pid.hpp"
#include "sensores.hpp"
#include "motores.hpp"
#include "fsm.hpp"

// VELOCIDADES  - PORCENTAJE DE PWM (0-100%)
/** @brief Límite máximo de velocidad de los motores (PWM %). */
const int32_t maxSpeed  = 90;  

/** @brief Velocidad variable para la rampa de aceleración inicial. */
int32_t velocidadAcel = 50;     

// SETPOINT y ZONA MUERTA
/** @brief Valor objetivo de lectura para estar centrado sobre la línea. */
uint16_t setpoint = 3500;       

/** @brief Margen de error aceptable alrededor del setpoint. */
uint16_t zonaMuerta = 50;      

/* // CONTROL IR - comentado por ahora
// ============================
// COMANDOS CONTROL
// ============================
#define CMD_ON_OFF   0x43           //Tecla 'play/pause'
#define RAW_ON_OFF   0xBC43FF00

void leer_IR() {
// Si recibe algo lo leemos/decodificamos
    if (IrReceiver.decode()) {
        // Guardamos los datos y separamos el dato crudo y el codigo
        auto data = IrReceiver.decodedIRData;
        uint8_t cmd  = data.command;

        // Si coinciden el codigo crudo y comando entonces arranco o paro el coche
        if (cmd == CMD_ON_OFF)   { RUN = !RUN;}

        // Liberamos
        IrReceiver.resume();
    }
}*/

/** @brief Array de punteros a funciones que vincula los estados con sus acciones. */
void (*acciones_estado[])() = { estadoStop, estadoAcel, estadoControl };

/** @brief Bandera para asegurar que la lógica de parada se ejecute una sola vez. */
bool stop_done = false;         


// ============================
// SETUP
// ============================
/**
 @brief Configuración inicial del microcontrolador.
 @details Inicializa periféricos (Serial, Buzzer, Motores, Sensores) y configura 
 las interrupciones y modos de pines.
 */
void setup() {
    // Inicializar Serial, Control-IR SOLOS SI se habilitaron en el PLATFORMIO.INI
    deb(Serial.begin(115200);)
    //control_ir( IrReceiver.begin(IR_PIN, ENABLE_LED_FEEDBACK);)
    
    // Configuracion buzzer
    setupBuzzer();
    
    // Configuracion motores - pines de direcion, canal de pwm, frecuencia y resolucion
    setupMotores();

    // Configuracion pines
    pinMode(ledMotores, OUTPUT);
    pinMode(ledCalibracion, OUTPUT);
    pinMode(BTN_RUN, INPUT);
    pinMode(BTN_STOP, INPUT);

    // Configuracion interrupciones
    setupInterrupciones(); 

    // Configuracion y calibracion de sensores
    setupSensores();
}


// ============================
// LOOP
// ============================
/**
 @brief Bucle principal del programa.
 @details Calcula la entrada combinada (RUN y SETPOINT) y llama a la FSM para 
 transicionar y ejecutar el estado correspondiente.
 */
void loop() {
    // Entrada de 2 bits (SETPOINT RUN - 00, 01, 10, 11) → 0, 1, 2, 3
    uint8_t c = (SETPOINT << 1) | RUN;

    // Realizamos la transicion y ejecutamos su estado 
    transicionar(c);
}


// ESTADO STOP - FUNCION DETENIDO
/**
 @brief Acción ejecutada en el estado de parada (STOP).
 @details Detiene los motores, apaga los LEDs de estado y reinicia la velocidad de aceleración.
 */
void estadoStop() {
    if (!stop_done) {                  // solo ejecuta una vez
        deb(Serial.println("Estado: STOP");)

        digitalWrite(ledMotores, LOW);
        digitalWrite(ledCalibracion, LOW);

        detenerMotores();
        
        velocidadAcel = 50;

        stop_done = true;
        deb(Serial.println("\n ---------------------- \n");)
    }
}


// ESTADO ACEL - FUNCION ACELERAR EN LINEA
/**
 @brief Acción ejecutada en el estado de aceleración (ACEL).
 @details Realiza un incremento progresivo de la velocidad mientras el robot se encuentre 
 dentro del setpoint para romper la inercia de manera suave.
 */
void estadoAcel() {
    deb(Serial.println("Estado: ACEL");)
    stop_done = false; // para que cuando vuelva a STOP se ejecute 1 vez
    
    // Leer posicion de línea (0 = extremo izquierda, 7000 = extremo derecha)  
    position = leerLinea();
    deb(Serial.printf("Posicion=%d\n", position);)

    // Incremento suave de velocidad
    if (velocidadAcel < maxSpeed) velocidadAcel++;

    // Mover motores con aceleracion progresiva
    moverMotores(velocidadAcel, velocidadAcel);

    // Indicador de que estamos en setpoint
    digitalWrite(ledCalibracion, HIGH);

    // Calculamos si estamos en el setpoint
    actualizarSP(position);

    // Reiniciamos las variables PID
    reiniciar_pid();

    deb(Serial.println("\n ---------------------- \n");)
}


// ESTADO CONTROL - FUNCION CONTROL EN LINEA
/**
 @brief Acción ejecutada en el estado de control activo (CONTROL).
 @details Ejecuta el algoritmo PID a intervalos fijos marcados por el temporizador 
 para corregir la trayectoria del robot sobre la línea.
 */
void estadoControl() {
    // Ejecutar solo cuando el timer indique el tick
    if (!has_expired) return;

    deb(Serial.println("Estado: CONTROL");)
    has_expired = false;    // ya paso un tick (timer isr) entonces debo reiniciarlo
    stop_done = false;      // cuando vuelva a STOP se ejecute 1 vez

    // Enceder led modo corredor
    digitalWrite(ledMotores, HIGH);

    // Apagar led cal - indicamos que no estamos en Setpoint 
    digitalWrite(ledCalibracion, LOW);

    // Leer posicion de línea (0 = extremo izquierda, 7000 = extremo derecha)    
    position = leerLinea();
    deb(Serial.printf("Posicion=%d\n", position);)

    // calculo la correccion para los motores segun la posicion y el delta tiempo (timer isr) 
    float correcion = calculo_pid(position, FIXED_DT_S);
 
    // Calculamos si estamos en el setpoint
    actualizarSP(position);

    // Control de motores
    controlMotores(correcion);

    // Mover los motores (Avanza, retrocede o para)
    moverMotores(motorSpeedIzq, motorSpeedDer);

    deb(Serial.println("\n ---------------------- \n");)
}

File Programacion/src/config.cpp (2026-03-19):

/**
 @file config.cpp
 @brief Implementación y asignación física de los pines del microcontrolador.
 @details Define la conexión de periféricos de interfaz, motores y el array de sensores.
 @author Legion de Ohm
 */

#include "config.hpp"


// ============================
// PINES - LEDS, BOTONES, BOCINA y SENSOR IR
// ============================
/** @brief Pin GPIO asignado al zumbador. */
const uint8_t pinBuzzer = 17;

/** @brief LED indicador para el estado de los motores. */
const uint8_t ledMotores = 13;

/** @brief LED indicador de finalización de calibración y estado de setpoint. */
const uint8_t ledCalibracion = 2;

/** @brief Pin del botón de inicio (SW par). */
const uint8_t BTN_RUN = 19;

/** @brief Pin del botón de parada (SW impar). */
const uint8_t BTN_STOP = 22;

/** @brief Pin reservado para el sensor infrarrojo (actualmente deshabilitado). */
//const uint8_t IR_PIN = 4;

// ============================
// CONFIGURACIÓN DE MOTORES
// ============================ 
/** @name Pines Motor Izquierdo */
///@{
const uint8_t motorPinIN1_Izq = 21;    ///< Control de dirección IN1.
const uint8_t motorPinIN2_Izq = 18;    ///< Control de dirección IN2.
const uint8_t motorPinSleep_Izq = 23;  ///< Pin de habilitación (Sleep).
///@}

/** @name Pines Motor Derecho */
///@{
const uint8_t motorPinIN1_Der = 26;    ///< Control de dirección IN1.
const uint8_t motorPinIN2_Der = 25;    ///< Control de dirección IN2.
const uint8_t motorPinSleep_Der = 16;  ///< Pin de habilitación (Sleep).
///@}

// ============================
// CONFIGURACIÓN SENSORES QTR & LINEA
// ============================
/** @name Asignación de Pines Array QTR */
///@{
const uint8_t S8 = 14;  ///< Sensor 8.
const uint8_t S7 = 27;  ///< Sensor 7.
const uint8_t S6 = 33;  ///< Sensor 6.
const uint8_t S5 = 32;  ///< Sensor 5.
const uint8_t S4 = 35;  ///< Sensor 4.
const uint8_t S3 = 34;  ///< Sensor 3.
const uint8_t S2 = 39;  ///< Sensor 2.
const uint8_t S1 = 36;  ///< Sensor 1.
///@}

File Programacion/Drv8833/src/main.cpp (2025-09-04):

#include <Arduino.h>
#include "drv8833.hpp"

// MOTOR IZQUIERDO
// Pines
const uint8_t motorPinIN1_Izq = 18;
const uint8_t motorPinIN2_Izq = 21;
const uint8_t motorPinSleep_Izq = 23;

// MOTOR DERECHO
// Pines
const uint8_t motorPinIN1_Der = 26;
const uint8_t motorPinIN2_Der = 25;
const uint8_t motorPinSleep_Der = 16;

// Canales PWM
const uint8_t motorPWM = 0; // Canal PWM 0
// Ajustes PWM
const uint32_t freqPWM = 10000; // Frecuencia del PWM = 10KHz
const uint8_t resPWM = 8;       // Resolución de 8 bits = 256 valores posibles [0, 255]

// Creación de dos objetos de la clase Motor
Drv8833 motorDer;
Drv8833 motorIzq;

void setup()
{
  // Ajustes iniciales del motor
  motorDer.setup(motorPinIN1_Der, motorPinIN2_Der, motorPinSleep_Der, motorPWM, freqPWM, resPWM);
  motorIzq.setup(motorPinIN1_Izq, motorPinIN2_Izq, motorPinSleep_Izq, motorPWM, freqPWM, resPWM);

}

void loop()
{
  // Mover los motores hacia adelante al 50% del PWM
  // Menor a 40% apenas se mueve                    [TODO:  Revisar por que pasa eso...]
  motorIzq.forward(50);
  motorDer.forward(50);
  delay(2000);

  // Detener motores
  motorIzq.stop();
  motorDer.stop();
  delay(20);

  // Mover los motores  hacia atras al 100% del PWM
  motorIzq.reverse(100);
  motorDer.reverse(100);
  delay(2000);

  // Detener motores
  motorIzq.stop();
  motorDer.stop();
  delay(1000);
}

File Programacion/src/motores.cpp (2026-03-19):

/**
 @file motores.cpp
 @brief Implementación de la capa de control de motores y manejo del driver DRV8833.
 @details Contiene la lógica para el control PWM de los motores, la gestión de dirección 
 (avance/reversa) y el cálculo de velocidades diferenciales basadas en la corrección PID.
 @author Legion de Ohm
 */

#include <Arduino.h>
#include "sensores.hpp"
#include "config.hpp"
#include "motores.hpp"
#include "pid.hpp"
#include "interrupciones.hpp"

/**
 @brief Constructor vacío de la clase Drv8833.
 */
Drv8833::Drv8833() {}

/**
 @brief Configura los pines de hardware y el periférico PWM del driver.
 @param pinIN1 Pin de dirección 1.
 @param pinIN2 Pin de dirección 2.
 @param pinSleep Pin de activación del driver.
 @param chPWM Canal ledc asignado.
 @param freqPWM Frecuencia del PWM.
 @param resPWM Resolución en bits del PWM.
 */
void Drv8833::setup(uint8_t pinIN1, uint8_t pinIN2, uint8_t pinSleep, uint8_t chPWM, uint32_t freqPWM, uint8_t resPWM) {
    _pinIN1 = pinIN1;
    _pinIN2 = pinIN2;
    _pinSleep = pinSleep;
    _chPWM = chPWM;
    _freqPWM = freqPWM;
    _resPWM = resPWM;

    pinMode(_pinIN1, OUTPUT);
    pinMode(_pinIN2, OUTPUT);
    pinMode(_pinSleep, OUTPUT);

    digitalWrite(_pinSleep, HIGH); // Habilitar driver

    ledcSetup(_chPWM, _freqPWM, _resPWM);
}

/**
 @brief Mueve el motor hacia adelante.
 @details Desvincula el pin IN2 del PWM y lo pone en LOW, mientras vincula IN1 al canal PWM.
 @param pPWM Porcentaje de potencia [0-100].
 */
void Drv8833::forward(uint8_t pPWM) {
    ledcDetachPin(_pinIN2); 
    digitalWrite(_pinIN2, LOW);      

    ledcAttachPin(_pinIN1, _chPWM);

    uint16_t maxDuty = (1 << _resPWM) - 1;
    uint16_t pwmDutyCycle = (maxDuty * pPWM) / 100;

    ledcWrite(_chPWM, pwmDutyCycle);  
}

/**
 @brief Mueve el motor hacia atrás.
 @details Desvincula el pin IN1 del PWM y lo pone en LOW, mientras vincula IN2 al canal PWM.
 @param pPWM Porcentaje de potencia [0-100].
 */
void Drv8833::reverse(uint8_t pPWM) {
    ledcDetachPin(_pinIN1);
    digitalWrite(_pinIN1, LOW);

    ledcAttachPin(_pinIN2, _chPWM);

    uint16_t maxDuty = (1 << _resPWM) - 1;
    uint16_t pwmDutyCycle = (maxDuty * pPWM) / 100;

    ledcWrite(_chPWM, pwmDutyCycle);
}

/**
 @brief Detiene el motor desvinculando ambos pines del PWM y poniéndolos en LOW.
 */
void Drv8833::stop() {
    ledcDetachPin(_pinIN1);
    ledcDetachPin(_pinIN2);

    digitalWrite(_pinIN1, LOW);
    digitalWrite(_pinIN2, LOW);
}

// ============================
// CONFIGURACIÓN DE MOTORES
// ============================

/** @brief Instancia estática para el motor izquierdo. */
static Drv8833 motorIzq;
/** @brief Instancia estática para el motor derecho. */
static Drv8833 motorDer;

/** @brief Canal PWM para motor izquierdo. */
static const uint8_t motorPWM_Izq = 0;
/** @brief Canal PWM para motor derecho. */
static const uint8_t motorPWM_Der = 1;

/** @brief Frecuencia de trabajo del PWM (20 kHz). */
static const uint32_t freqPWM = 20000; 
/** @brief Resolución del PWM (8 bits). */
static const uint8_t  resPWM  = 8;     

/** @brief Almacena la velocidad calculada para el motor izquierdo. */
int32_t motorSpeedIzq = 0;
/** @brief Almacena la velocidad calculada para el motor derecho. */
int32_t motorSpeedDer = 0;

/**
 @brief Inicializa el hardware de ambos motores y los detiene inicialmente.
 */
void setupMotores() {
    motorDer.setup(motorPinIN1_Der, motorPinIN2_Der,
                   motorPinSleep_Der, motorPWM_Der,
                   freqPWM, resPWM);

    motorIzq.setup(motorPinIN1_Izq, motorPinIN2_Izq,
                   motorPinSleep_Izq, motorPWM_Izq,
                   freqPWM, resPWM);

    detenerMotores();
}

/**
 @brief Aplica las velocidades a los motores traduciéndolas a comandos del driver.
 @details Evalúa el signo de la velocidad para decidir si aplicar forward, reverse o stop.
 @param motorSpeedIzq Velocidad para el motor izquierdo (positivo = avance).
 @param motorSpeedDer Velocidad para el motor derecho (positivo = avance).
 */
void moverMotores(int32_t motorSpeedIzq, int32_t motorSpeedDer) {
    deb(Serial.printf("MotorIzq=%d\n", motorSpeedIzq);)
    deb(Serial.printf("MotorDer=%d\n", motorSpeedDer);)

    if      (motorSpeedIzq > 0) {   motorIzq.forward(motorSpeedIzq);        }
    else if (motorSpeedIzq < 0) {   motorIzq.reverse(abs(motorSpeedIzq));   }
    else                        {   motorIzq.stop();    }

    if      (motorSpeedDer > 0) {   motorDer.forward(motorSpeedDer);        }
    else if (motorSpeedDer < 0) {   motorDer.reverse(abs(motorSpeedDer));   }
    else                        {   motorDer.stop();    }   
}

/**
 @brief Envía la señal de parada a ambos motores.
 */
void detenerMotores(){
    motorIzq.stop();
    motorDer.stop();
}

/**
 @brief Actualiza la bandera de Setpoint basada en la proximidad de la posición al centro.
 @param pos Posición actual detectada por los sensores.
 */
void actualizarSP(uint16_t pos) {
    SETPOINT = (abs(pos - setpoint) < zonaMuerta);
}

/**
 @brief Calcula las velocidades individuales aplicando la corrección diferencial.
 @details Si el robot está fuera de la zona muerta, ajusta las velocidades base 
 sumando o restando la corrección y limita los valores al rango @f$ \pm @f$maxSpeed.
 @param correcion Valor de corrección obtenido del PID.
 */
void controlMotores(float correcion) {
    if ( !SETPOINT ) {
        motorSpeedIzq = baseSpeed - correcion;
        motorSpeedDer = baseSpeed + correcion;

        motorSpeedIzq = constrain(motorSpeedIzq, -maxSpeed, maxSpeed);
        motorSpeedDer = constrain(motorSpeedDer, -maxSpeed, maxSpeed);
        return;
    }

    SETPOINT = true;
}

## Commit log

2025-08-25 V1 - Primer commit.
    [COCHE_COMPETENCIA.kicad_pcb, COCHE_COMPETENCIA.kicad_sch, puente_H.kicad_pcb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]
2025-08-28 V1 - MotorBoard 2025
    [COCHE_COMPETENCIA.kicad_pcb, COCHE_COMPETENCIA.kicad_sch, MATRIZ_COCHE_COMPETENCIA.kicad_pcb]
2025-08-31 Added Coche de Competencia.drawio
2025-08-31 V1 - Diagrama Draw.io y Mejoras documentacion
    [COCHE_COMPETENCIA.kicad_pcb, MATRIZ_COCHE_COMPETENCIA.kicad_pcb, puente_H.kicad_pcb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]
2025-08-31 V1 - Reestructuracion de carpetas + incorporacion de galeria
    [COCHE_COMPETENCIA.kicad_pcb, COCHE_COMPETENCIA.kicad_sch, MATRIZ_COCHE_COMPETENCIA.kicad_pcb]
2025-09-04 V1.1 - Correccion de bocina y programas de motores.
    [COCHE_COMPETENCIA.kicad_pcb, COCHE_COMPETENCIA.kicad_sch]
2025-09-04 V1.1 - Programa de Buzzer + Modulo Drv8833
    [COCHE_COMPETENCIA.kicad_pcb]
2025-09-04 V1.1 - Reordenamiento de carpetas
2025-09-09 V1.2 - Mejoras de PCB: alimentacion, bocina y borneras.
    [COCHE_COMPETENCIA.kicad_pcb, COCHE_COMPETENCIA.kicad_sch, COCHE_COMPETENCIA.step]
2025-09-09 Add files via upload
    Prueba de Sensores - 09Sep25
2025-09-09 Primer commit: sensores y motores
2025-09-10 V1.3 - Diodo de proteccion + Mejor ubicacion de Sw's
    [COCHE_COMPETENCIA.kicad_pcb, COCHE_COMPETENCIA.kicad_sch, MATRIZ_COCHE_COMPETENCIA.kicad_pcb]
2025-09-14 V1.3 - Agregado de Prot. Tension inversa & pull downs y acomodado de componentes.
    [COCHE_COMPETENCIA.kicad_pcb, COCHE_COMPETENCIA.kicad_sch]
2025-09-24 V1.3 - Protecciones
    [MATRIZ_COCHE_COMPETENCIA.kicad_pcb]
2025-09-24 BaronRojo prueba del 23Sep25
    Prueba de código base en funcionamiento
2025-10-01 V1.4 - Mejores pistas & Modulo de Interrupciones
    [COCHE_COMPETENCIA.kicad_pcb, COCHE_COMPETENCIA.kicad_sch, MATRIZ_COCHE_COMPETENCIA.kicad_pcb]
2025-10-03 Nightfall Condor - Ajustar PID, flujo de programa y bocina/calibracion
2025-10-04 Nightfall Condor - Flujo y Bocina TODO modulo pid.
2025-10-04 Nightfall Condor - PID precompetencia.
2025-10-07 Nightfall Condor PreComp - Varios errores.
    [main.cpp]
2025-10-17 V1.4 - Programa PID seguidor
2025-10-29 V1.4 - Programa seguidor Modular
    [COCHE_COMPETENCIA.kicad_pcb, COCHE_COMPETENCIA.kicad_sch, Motores Kicad.kicad_pcb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]
2026-03-19 V2.0 - Nueva version Seguidor De Linea
    [5104--3DModel-STEP-630548.STEP, 5104.step, ARDUINO_NANO.step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]
2026-03-20 Agregado de Pcb Futboleros V1.5
    [COCHE_COMPETENCIA.kicad_pcb, COCHE_COMPETENCIA.kicad_sch, COCHE_COMPETENCIA.step]
